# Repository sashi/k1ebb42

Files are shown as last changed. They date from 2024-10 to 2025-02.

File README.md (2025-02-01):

These instructions help you setup your K1 with EBB42 v1.1, v.1.2 using M5P - No need U2C  
Thanks to EricZimmerman [guides](https://github.com/EricZimmerman/VoronTools/tree/main) and Maz0r [work](https://github.com/maz0r/klipper_canbus)  
Thanks to Toxa#7441 ([anarhyst266](https://github.com/Anarhyst266)) on Discord for making the adapter and fan cover

## BOM
EBB42    
2x M3 Heatset Inserts (OD 4.2mm x L 3mm) (For BootyBurner 5015)    
4x M2 Heatset Inserts (OD 3mm x L 3mm) (For EBB42)  
4x M2 x 3mm flat head screws  
2x M3 x 20mm screws  
5015 24v Fan (I recommend Sunon/GDSTIME/Honeybadger)    
Toxas adapter & fan cover ([ebb42_mount.step](https://github.com/sashi/k1ebb42/blob/main/step/ebb42_mount.step) & [BootyBurner_5015.stl](https://github.com/sashi/k1ebb42/blob/main/step/BootyBurner_5015.stl))

## Network 
1. Use nano to create a new file with the command sudo nano /etc/network/interfaces.d/can0  
2. Add the following code  
```
allow-hotplug can0
iface can0 can static
 bitrate 1000000
 up ifconfig $IFACE txqueuelen 1024
 pre-up ip link set can0 type can bitrate 1000000
 pre-up ip link set can0 txqueuelen 1024
```
3. Save the file with CTRL-o, ENTER, CTRL-x and reboot the pi with sudo reboot  
4. Verify the network via ip -s link show can0 which should reflect that the CAN network is UP

## M5P
1. Clone Katapult to your Pi  

```
cd ~  
git clone https://github.com/Arksine/katapult
```  
2. Run the following commands to bring up the menu to configure the firmware  
```
cd katapult
make menuconfig
```  
3. Starting from the top, make your firmware selections look exactly like the image below  
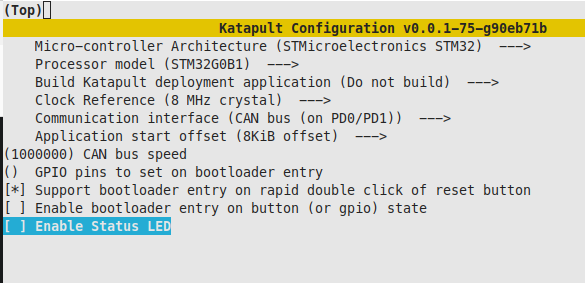
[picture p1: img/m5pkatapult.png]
m5pkatapult
  
4. Exit using ESC or Q, then confirm with yes (Y)  
5. Build the firmware using the following commands:  
```
make clean
make
```
If no errors continue  
6. Run the following commands to bring up the menu to configure the firmware (Klipper)
```
cd ~/klipper
make menuconfig
```
7. Starting from the top, make your firmware selections look exactly like the image below
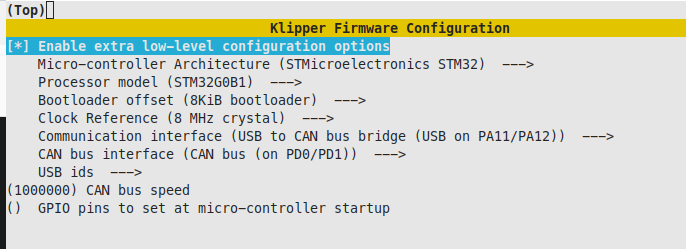
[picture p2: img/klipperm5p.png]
klipperm5p
  
8. Exit using ESC or Q, then confirm with yes (Y)  
9. Build the firmware using the following commands:
```
make clean
make
```
If no errors continue  

## Flashing Klipper to M5P
1. With power on the M5P side of the board, press and hold down the boot button then click the reset button, allow a secund or two to pass then release the boot button  
2. Run ``lsusb``  
3. Look for STM in DFU Mode in the output text then proceed, if not try step 1 again  
4. Run the following to flash katapult to M5P  
```
sudo dfu-util -a 0 -D ~/katapult/out/canboot.bin --dfuse-address 0x08000000:force:mass-erase -d 0483:df11
```
If no errors proceed  (If you see any mention of an error after the File downloaded successfully message, it can be ignored)  
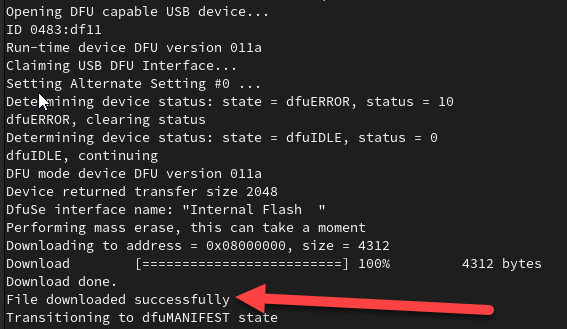
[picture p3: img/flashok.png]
flashok


5. Run the following to flash klipper to M5P
```
sudo dfu-util -a 0 -D ~/klipper/out/klipper.bin --dfuse-address 0x08002000:leave -d 0483:df11
```
If no errors proceed and click the reset button  the M5P (If you see any mention of an error after the File downloaded successfully message, it can be ignored>  
flashok

## Building and Flashing for EBB42

1. Run the following commands to bring up the menu to configure the firmware  
```
cd ~/katapult
make menuconfig
``` 

2. Starting from the top, make your firmware selections look exactly like the image below  
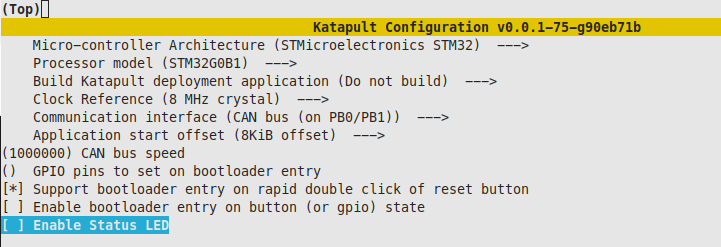
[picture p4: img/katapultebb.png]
katapultebb
  
3. Exit using ESC or Q, then confirm with yes (Y)  
4. Build the firmware using the following commands:  
```
make clean
make
```
If no errors continue  

5. Run the following commands to bring up the menu to configure the firmware  (Klipper)
```
cd ~/klipper
make menuconfig
``` 
6. Starting from the top, make your firmware selections look exactly like the image below  
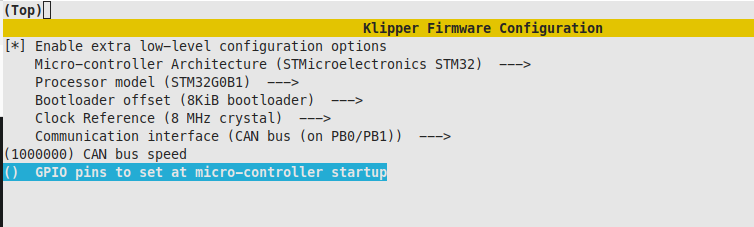
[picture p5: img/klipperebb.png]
klipperebb
  
4. Plug in a USB-C cable from the EBB42 to your Pi and set the USB jumper
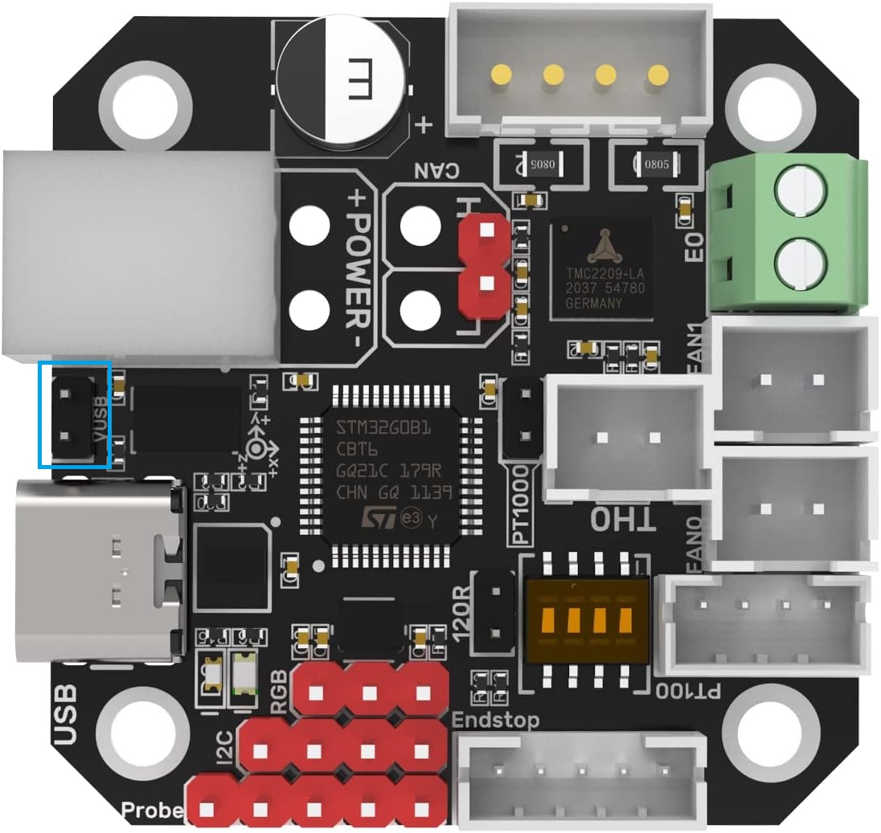
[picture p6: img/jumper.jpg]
jumper
  
5. Hold down the boot button and press the reset button, wait a second or two and then release the boot button  
6. Run ``lsusb``  
7. Look for STM in DFU Mode in the output text then proceed, if not try step 2 again  
8. Run the following to flash Katapult to EBB42
```
sudo dfu-util -a 0 -D ~/katapult/out/canboot.bin --dfuse-address 0x08000000:force:mass-erase -d 0483:df11
```
If no errors proceed and click the reset button  the M5P (If you see any mention of an error after the File downloaded >  message, it can be ignored.  
flashok
9. Disconnect USB-C cable and remove the jumper
10. Place a jumper on the 120R header on the EBB42  
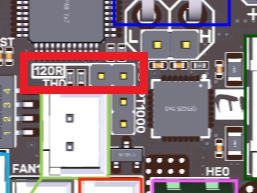
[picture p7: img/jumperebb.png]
jumperebb


## Wiring
1. Disconnect all power  
2. Crimp the required wires to the molex connector on the EBB42  
3. ***Triple check your VIN, GND, CAN_H, CAN_L match the connector side on the EBB and on the M5P side***  
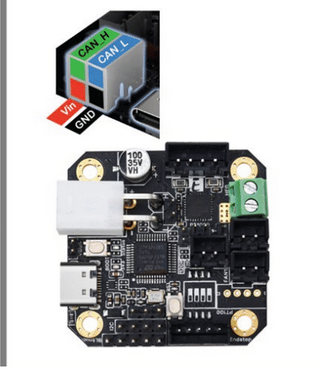
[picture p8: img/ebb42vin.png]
ebb42vin
  
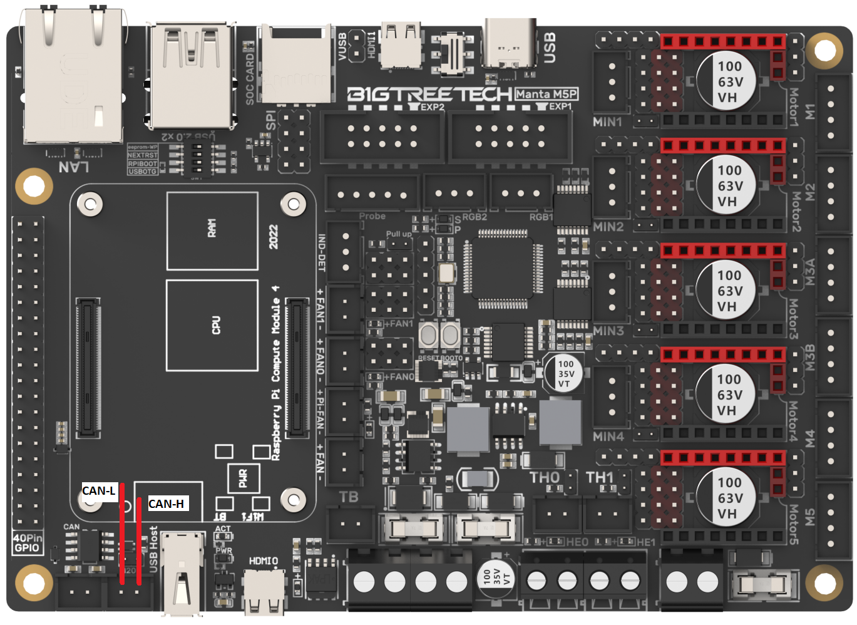
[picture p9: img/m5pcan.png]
m5pcan
  
4. Place a jumper on the 120R header on the M5P  
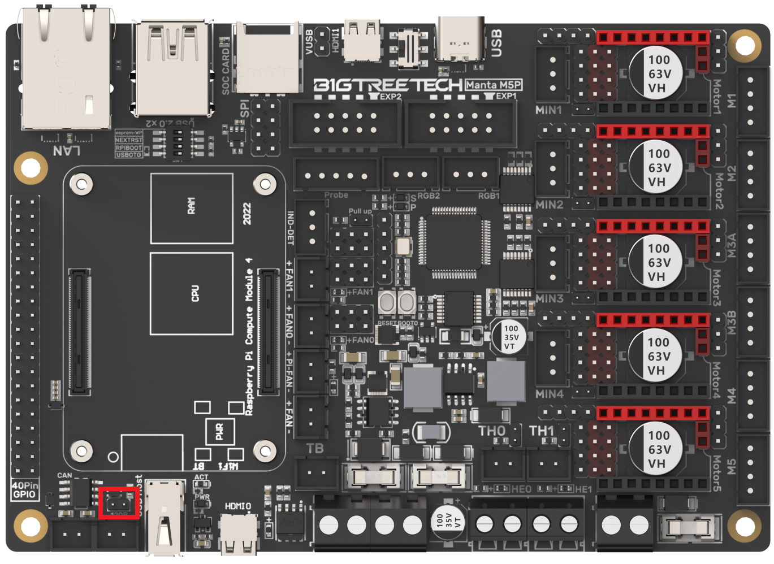
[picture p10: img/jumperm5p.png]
jumperm5p
  

## Flashing Klipper to EBB42
1. Find your UUID  
```
sudo service klipper stop
python3 ~/katapult/scripts/flashtool.py -i can0 -q
```
2. It should return something like: ***(Take note of the UUID that has "Application: Klipper. This is your UUID you will need for your M5P)***
```
"Detected UUID: XXXXXXXXXX, Application: Katapult"
```
3. Record the UUID. This is YOUR uuid and will be used for the next step and in your cfg files  
4. Now its time to flash klipper via CAN! Run the following command, substituting your uuid: 
```
python3 ~/katapult/scripts/flashtool.py -i can0 -u b6d9de35f24f -f ~/klipper/out/klipper.bin
```
5. The EBB will be flashed and you should see a message about success, etc. Request for uuids again via:  
```
python3 ~/katapult/scripts/flashtool.py -i can0 -q
```
but now, notice how it shows Klipper for the application! Yay!  

6. Restart klipper via  
```
sudo service klipper start
```

## Config
1. For your M5P - you should now replace your serial with canbus_uuid: <your M5P UUID that you got in the previous step, step 2>  
2. For your EBB42 - your UUID is the one you got in step 5

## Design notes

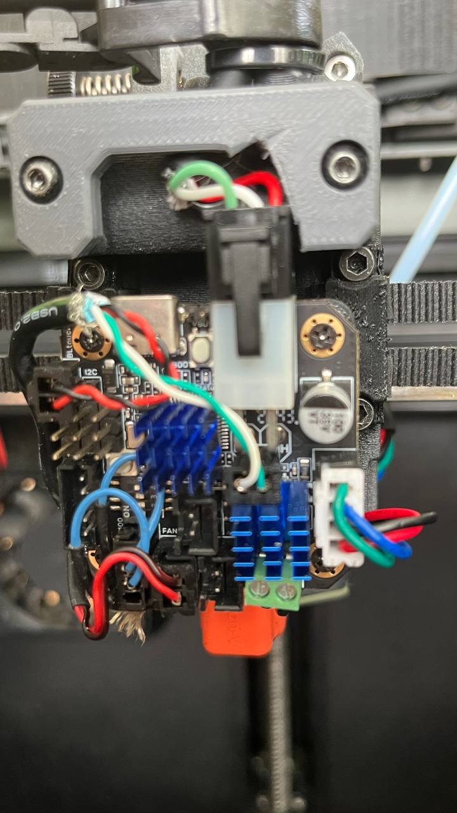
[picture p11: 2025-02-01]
img/ebb_connect.jpg

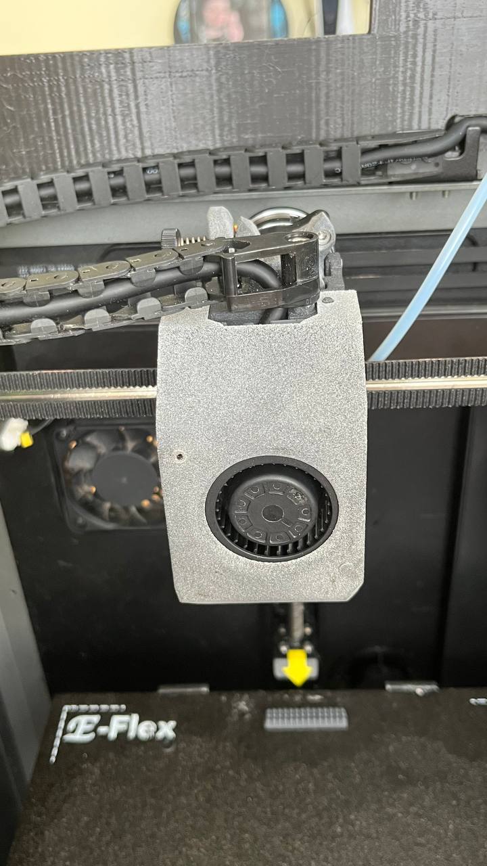
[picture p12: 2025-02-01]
img/complete_head.jpg

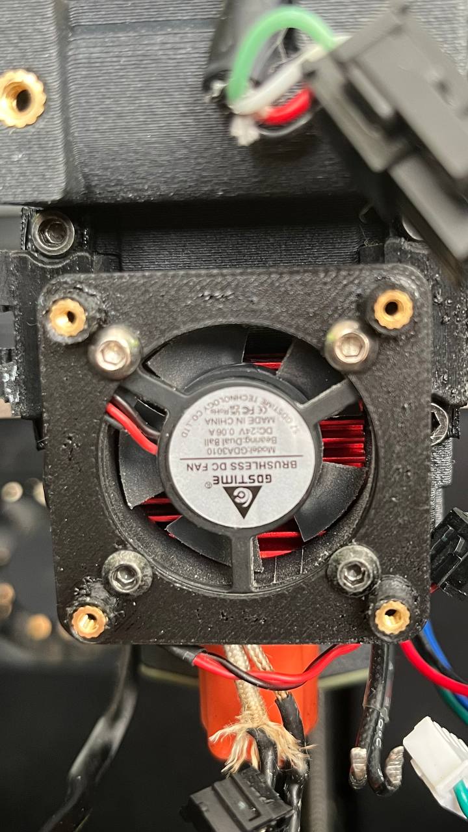
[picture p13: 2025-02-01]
img/mount.jpg

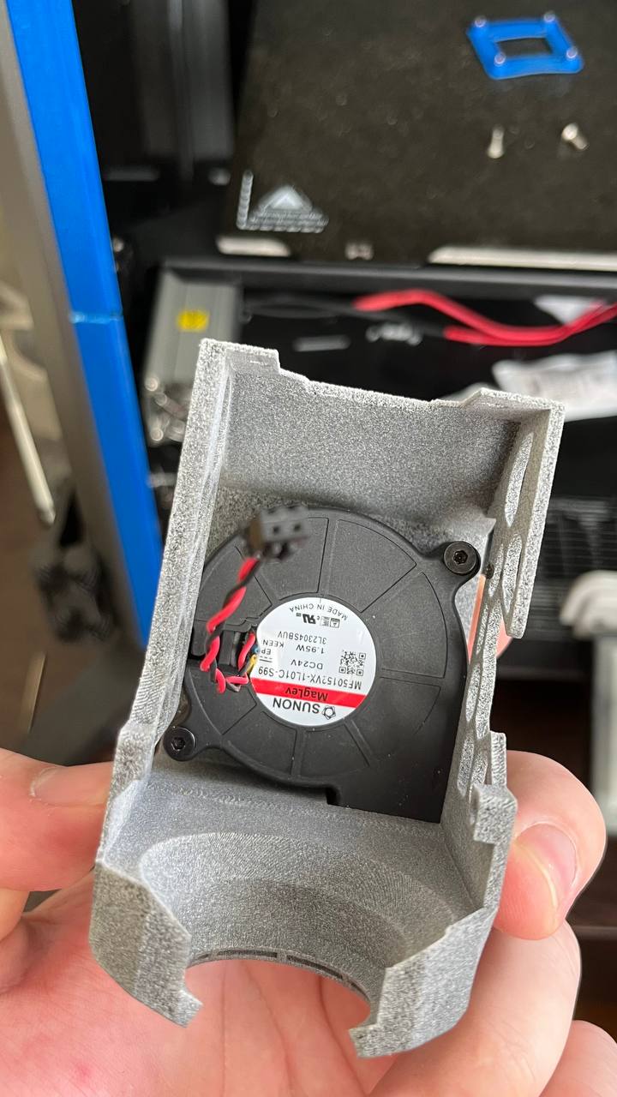
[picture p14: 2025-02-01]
img/fan5015.jpg

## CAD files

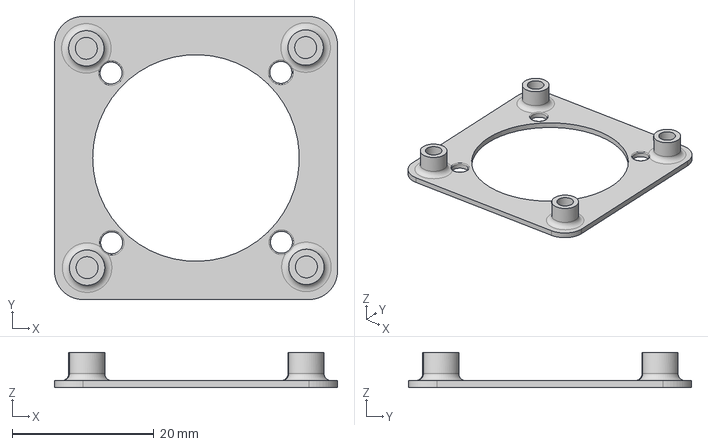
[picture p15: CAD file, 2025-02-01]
step/ebb42_mount.step
40.0 x 40.0 x 5.00 mm

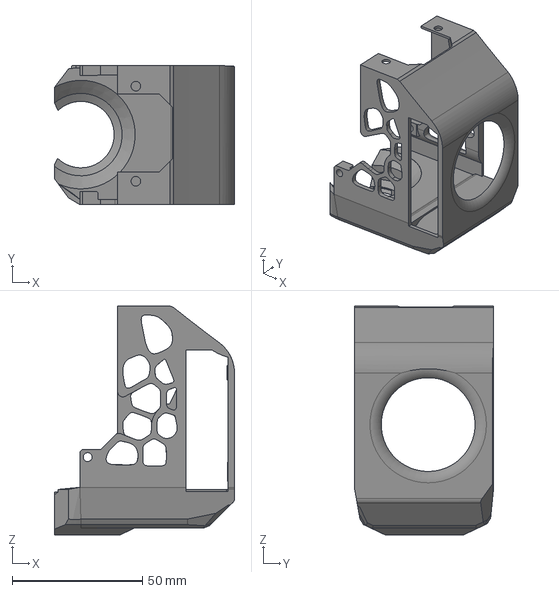
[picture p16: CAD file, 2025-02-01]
step/BootyBurner_5015_linear_gantry.step
69.1 x 53.5 x 87.9 mm

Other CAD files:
step/BootyBurner_5015_stock_gantry.step
step/BootyBurner_5015_linear_gantry.stl
step/BootyBurner_5015_stock_gantry.stl

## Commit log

2024-10-10 Steps & STL
    [BootyBurner_5015.step, BootyBurner_5015.stl, ebb42 v1.step]
2025-01-13 Updated readme + stl
    [BootyBurner_5015.stl]
2025-02-01 fixed toolhead model for better cooling. Added model for stock gantry
    [BootyBurner_5015.step, BootyBurner_5015.stl, BootyBurner_5015_linear_gantry.step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]
